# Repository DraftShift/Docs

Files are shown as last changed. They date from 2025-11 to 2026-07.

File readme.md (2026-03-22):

# DraftShift Documentation Source

This repository contains the source code for the DraftShift documentation website.

Visit [https://stealthchanger.com](https://stealthchanger.com) for the actual documentation.

---

## Contributing

We welcome contributions! If you'd like to help improve the documentation:

- Submit a descriptive [pull request](https://docs.github.com/en/pull-requests/collaborating-with-pull-requests/proposing-changes-to-your-work-with-pull-requests/creating-a-pull-request) of the feature/issue you are addressing.

- Keep the documented information concise.

### Contributing Build Guides

If you want to contribute build guides, please refer to the [Build Guide documentation](CONTRIBUTING_GUIDES.md) for more information.

### Development Setup

To run the documentation site locally:

1. **Prerequisites**: Ensure Python is installed and included in your environment PATH.

2. **Install dependencies**:
   ```
   pip install -r requirements.txt
   ```

3. **Run the development server**:
   ```
   python -m mkdocs serve
   ```

The site will be available at `http://127.0.0.1:8000` with live reload enabled.

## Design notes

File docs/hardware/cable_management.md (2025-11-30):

---
search:
  boost: 2 
---

## Umbilical Cables
An umbilical cable is required for each toolhead. They typically route from a [distribution board](../electronics/distro_boards.md) to a [toolhead board](../electronics/th_boards.md). On a StealthChanger, keeping the tool's umbilical in a controlled state is extremely important. If a tool's umbilical were to obstruct any of the other tools, it could result in a crash and cause a print failure. 

To help the umbilical move in a controlled fashion, we employ the use of a flat spring steel or piano wire. This addition gives the umbilical a controlled arc and helps it return to its resting position safely.

!!! tip "Spring Steel?"
    Flat spring steel (3x0.3mm) is the preferred aid for the tool's umbilical. It provides better lateral control and is what comes supplied as part of the LDO `Toolhead and Dock Kit`.

Umbilical Cables

## Fanny Pack
Originally by [ManCheetah](https://www.printables.com/@EddieSha_454383){:target="_blank"}, the Fanny Pack has been adopted by DraftShift Design as the de facto method of housing a [distribution board](../electronics/distro_boards.md) on the rear of the printer. Compared to the original, our updated version brings compatibility with a number of [distribution boards](../electronics/distro_boards.md) and buck converter options.

Fanny Pack

## Wire Duct
The Wire Duct serves as a conduit between the [Fanny Pack](#fanny-pack) and your printers electronics bay. Under its cover is an EMS compatible panel for you to mount any extra pieces you might need. 

Wire Duct

## Assembly
See the [Build Guides](../hardware/guides/cable_management/index.md) for assembly instructions.

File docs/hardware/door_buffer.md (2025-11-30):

---
search:
  boost: 2 
---

Door Buffer

## Context

### The Problem
To give the [Modular Docks](modular_dock.md) the maximum amount of rigidity, they need to be supported above and below. Adding an extrusion [crossbar](#crossbar) solves that problem but also introduces another. With the crossbar in line with the frame, the standard Voron V2 front-idlers collide with the crossbar and moving the extrusion outside of the frame would get in the way of mounting the door.

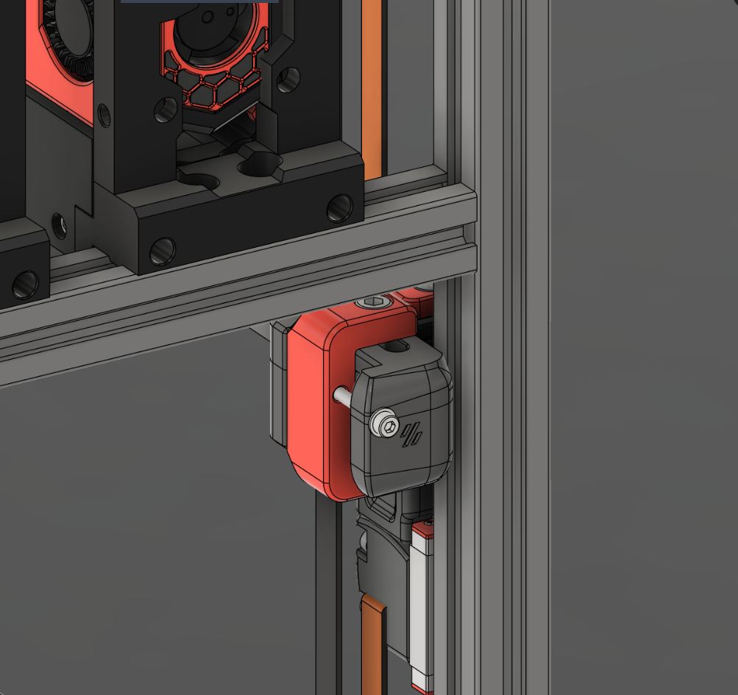
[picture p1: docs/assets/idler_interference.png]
Idler interference


### The Solution
Adding a Door Buffer provides a means to install the [crossbar](#crossbar) and retain the ability to mount the door on the front. The Door Buffer uses 3d printed pieces to fill the gaps around the front of the printers frame and adds new mounting points for the door.

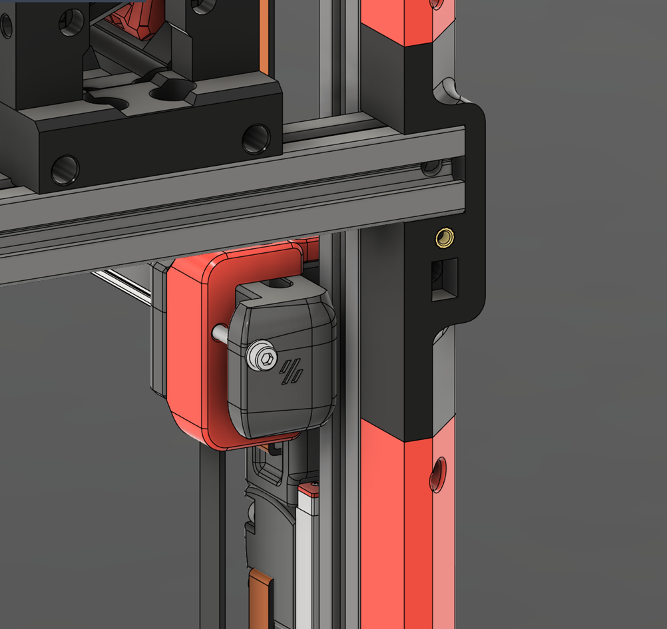
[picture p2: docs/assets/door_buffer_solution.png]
Door buffer solution


There are versions of the Door Buffer for both [standard Voron V2 doors](https://github.com/DraftShift/DoorBuffer/tree/main/STL/Stock%20Voron){:target="_blank"} and the [ClickyClack Fridge Door Mod](https://github.com/DraftShift/DoorBuffer/tree/main/STL/Clicky-Klack){:target="_blank"}, as well as options for [Micron](https://github.com/DraftShift/DoorBuffer/tree/main/STL/Micron){:target="_blank"}.

!!! info "Alternatives"
    You don't necessarily need to use printed pieces to act as a buffer. There are some other methods that the community uses.

    * **2020/1515 Extrusion** - Using blind joints you can mount extrusion to the front of the frame essentially making it 4020/3015.
    * **4020/3015 Extrusion** - Build the front of your printers frame using larger extrusion. 
    * **Mini/Micro BFI** - [Mini/Micro BFI](https://github.com/DraftShift/StealthChanger/tree/main/UserMods/BT123/MiniBFI%20%2B%20MicroBFI){:target="_blank"} takes a different approach and shortens the BFI idlers. This means the [crossbar](#crossbar) can be kept within the printers frame at the cost of less printable area and reduces the amount you can adjust the AB belts.

## Crossbar
The crossbar is a piece of extrusion mounted to the front of the printer’s frame, providing a rigid and stable attachment point for the [Modular Dock](modular_dock.md).

The crossbar should be made from extrusion that matches your printer, 2020 for Voron V2 or 1515 for Micron. The length of the crossbar changes depending on the size of your frame and which version of Door Buffer you are using.

| Printer | DraftShift Crossbar | LDO Crossbar |
| --- | --- | --- |
| Voron 250 | 400mm | 370mm |
| Voron 300 | 450mm | 420mm |
| Voron 350 | 500mm | 470mm |
| Micron 180 | 302mm | - |

!!! tip "Crossbar Adapter"
    You can use the DraftShift Door Buffer with LDO length extrusions by using an [adapter](https://github.com/DraftShift/DoorBuffer/tree/main/STL/Adaptor){:target="_blank"}.

!!! info "Monolith AWD"
    With Monolith protrusion the front motors would hit the crossbar even with the door-buffer. To work around that you can use one of the following usermods:

    - [printed adapter for door buffer with crossbar and Monolith AWD](https://github.com/DraftShift/DoorBuffer/tree/main/UserMods/MikeYankeeOscarBeta/Doorbuffer_Adapters){:target="_blank"}
    
    - [printed adapter for crossbar with doomcube 4040 frame and Monolith AWD](https://github.com/DraftShift/ModularDock/tree/main/UserMods/MikeYankeeOscarBeta/Monolith_Crossbar){:target="_blank"}

## Assembly
The assembly guide for the Door Buffer can be found in the [Build Guides](guides/door_buffers/index.md) section.

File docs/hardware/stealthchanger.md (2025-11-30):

---
search:
  boost: 2 
---

StealthChanger is the key component and namesake of the StealthChanger ecosystem. It can be broken down in to 2 main components, the [Shuttle](#shuttle) and [Backplate](#backplate), which allows the toolhead to be removed from the gantry and be docked so that another tool can be picked up. During operation, the mechanism also behaves like [Voron Tap](https://github.com/VoronDesign/Voron-Tap){:target="_blank"} and can be used for probing the bed.

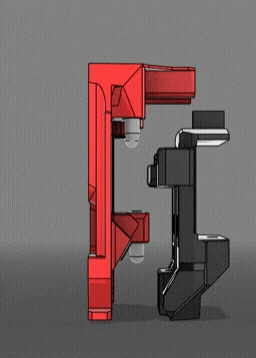
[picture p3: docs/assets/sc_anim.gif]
StealthChanger


## Shuttle
The StealthChanger Shuttle gets mounted to the gantry's X-rail MGN carriage and serves the purpose of being a receptacle for the [Backplate](#backplate). It uses bushings and magnets which allow the [Backplate](#backplate) to
kinematically attach to the gantry.

### Printed vs CNC
The printed and CNC versions of the Shuttle both operate in the same way. You can print the shuttle and source the bushings, magnet and screws or purchase a ready to go CNC shuttle. 

CNC Shuttles offer some QOL improvements like improved belt retention and in the case of LDO's Shuttle, precision-machined bushings.

When printing a Shuttle, it is important to note that the selection of material you use and your printers accuracy are important. Please reference the [Print Tuning Section](../getting_started.md#print-tuning) before printing your Shuttle.

!!! warning "ABS+"
    We have found that when used for StealthChanger, ABS+ tends to crack over time and advise against using it.

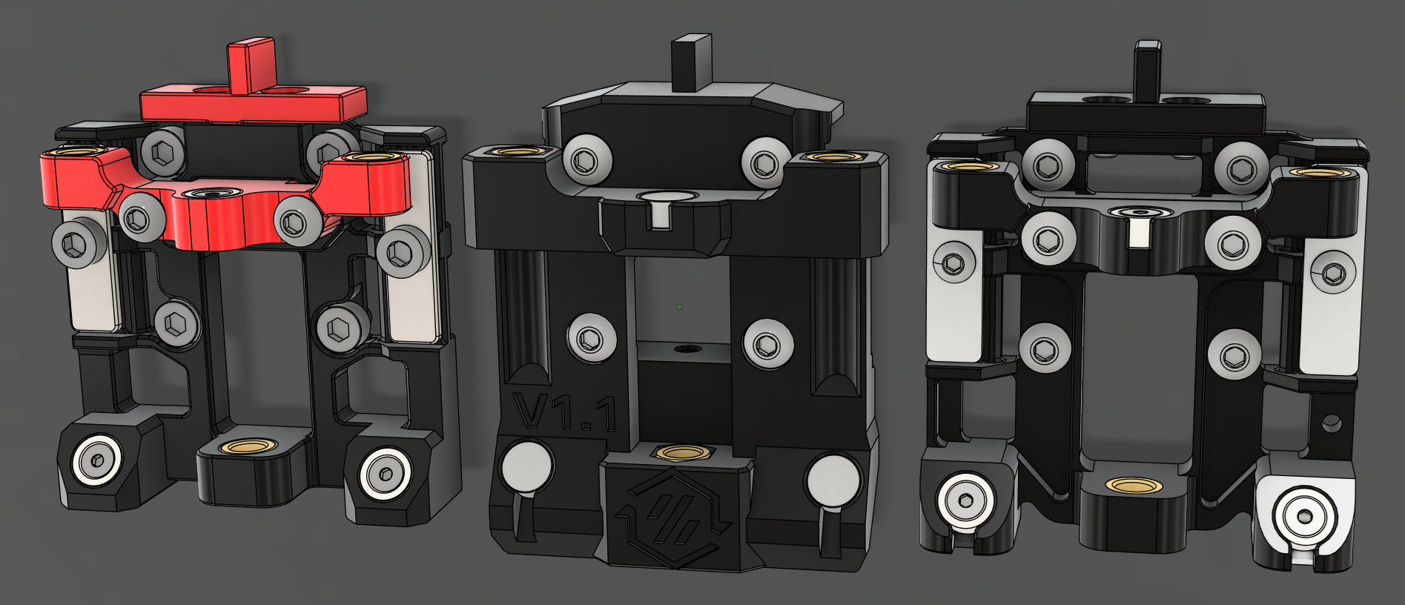
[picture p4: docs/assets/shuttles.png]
Shuttles


| Shuttle | MGN12 | MGN9 | Micron | 6mm Belt | 9mm Belt |
| :-: | :-: | :-: | :-: | :-: | :-: |
| Printed | :fontawesome-solid-check:{style="color:green;"} | :fontawesome-solid-asterisk:{style="color:orange;"} | :fontawesome-solid-asterisk:{style="color:orange;"} | :fontawesome-solid-check:{style="color:green;"} | :fontawesome-solid-asterisk:{style="color:orange;"} |
| CNC | :fontawesome-solid-check:{style="color:green;"} | :fontawesome-solid-xmark:{style="color:red;"} | :fontawesome-solid-xmark:{style="color:red;"} | :fontawesome-solid-check:{style="color:green;"} | :fontawesome-solid-check:{style="color:green;"} |

!!! asterisk "MGN9/Micron"
    The hole spacing on MGN9 is too small to clamp the belts reliably without the screws getting in the way. This means a Voron V2 with MGN9 on X axis or a Micron requires the use of the [Shuttle Keeper](#shuttle-keeper). 

!!! asterisk "9mm belts"
    9mm belts can be used with CNC Shuttles. If you want to use 9mm belts with a printed Shuttle, a [usermod by BT123](https://github.com/DraftShift/StealthChanger/tree/main/UserMods/BT123/Split%20Keeper){:target="_blank"} is required.

!!! info "Monolith and Inverted Belts"
    Inverted belts with printed shuttle require the use of this [usermod by BT123](https://github.com/DraftShift/StealthChanger/tree/main/UserMods/BT123/Split%20Keeper){:target="_blank"}.
    Inverted belts can be mounted to CNC Shuttle as is, but with [Monolith](https://github.com/Monolith3D/Monolith_Gantry/tree/main){target="_blank"} this results in slight angled belt-path. To get a straight belt path with CNC-shuttle you can either use [belt-lock](https://github.com/MikeYankeeOscarBeta/belt_lock){:target="_blank"} or this [XY-joint mod by dderg](https://github.com/Monolith3D/Monolith_Gantry/tree/main/UserMods/dderg/XY%20Joints%20compatible%20with%20Fysetc%20CNC%20Stealthchanger%20Shuttle){:target="_blank"}.

## Shuttle Keeper
The Shuttle Keeper is an additional component that can be used to hold the belts in place while the [Shuttle](#shuttle) is removed from the MGN Rail. There are situational reasons as to when and why you would want to use a Shuttle Keeper. See the below list for details.

* Only compatible with a printed [Shuttle](#shuttle).
* Required for a MGN9 [Shuttle](#shuttle).
* Optional for a MGN12 [Shuttle](#shuttle).
* Shuttle Keeper moves the toolhead forward 5-6mm.

Shuttle Keeper

## Belt Helper
Belt helper is a tool that will hold your belts for you while installing the [Shuttle](#shuttle). Once attached to the belts, the Belt Helper will assist in pulling the belts into position for the [Shuttle](#shuttle) to clamp them.

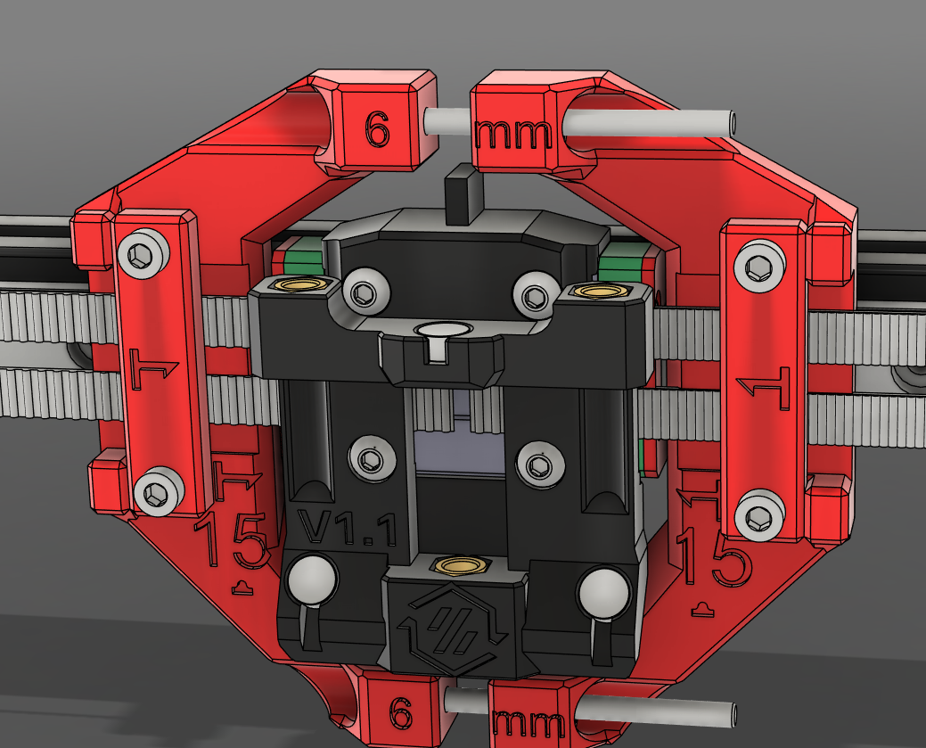
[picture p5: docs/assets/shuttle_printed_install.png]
Shuttle Install


!!! tip "One Tool to Rule Them All"
    The Belt Helper was designed to assist with installing the printed [Shuttle](#shuttle). It can also be useful with CNC shuttles to give you that extra set of hands you always wanted.

!!! info "Mini/Micro BFI"
    If using [Mini/Micro BFI](https://github.com/DraftShift/StealthChanger/tree/main/UserMods/BT123/MiniBFI%20%2B%20MicroBFI){:target="_blank"}, the Belt Helper is required to pre tension your belts to a point where your idlers only need minimal adjustment.

## Backplate
The StealthChanger Backplate is the companion component to the [Shuttle](#shuttle). Each compatible toolhead has its own unique Backplate that gets attached to the tool. The backplate is a critical component of StealthChanger and requires you to ensure you have good print accuracy, especially when pairing with a CNC Shuttle. Please reference the [Print Tuning Section](../getting_started.md#print-tuning) before printing your Backplate. For a list of compatible tools, see the [Toolheads](toolheads.md) page.

Backplate

## Assembly
See the [Shuttle Build Guides](guides/shuttles/index.md) and [Backplate Build Guides](guides/backplates/index.md) sections for assembly instructions.

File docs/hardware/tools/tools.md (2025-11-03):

For the purposes of StealthChanger the toolhead selection is rather important. It is often the deciding factor in how the rest of the build is configured. It determines which docks you can use, the maximum number of tools you can use, and the can also have a large impact on power requirements.

???+ info "Printing"
    Officially supported toolheads do not require modification to work with StealthChanger, only the addition of the Stealthchanger backplate and possibly a spacer. Each toolhead can be sourced from their respective repositories. Toolheads that are not officially supported will require modification to work with StealthChanger and will be marked as a usermod.

??? info "Extruders"
    * You can use any extruder you want as long as it is supported by the toolhead of your choice.
    * It's important to note that the width of the extruder may impact the maximum tool count as it may render the tool width wider, potentially limiting the total number of tools that can be accommodated.
    * :warning: Pay attention to the tensioning screw on the extruder, it may collide with the tool beside it if it extends outside the tool's width and there is not enough room between them.

??? info "Hotends"
    * Choose whichever hotend you like, as long as the toolhead supports it, you can use it.
    * :warning: Some high-flow hotends may require significant tuning to prevent oozing while moving to, and from the dock.

??? tip "Community Recommendation"
    Anthead is the recommended toolhead due to its integrated magnets in the fan ducts, which enhance stability during the docking process. Other tools can achieve similar results, but may require additional modifications.

<div class="grid cards" style="text-align: center;" markdown>

{% for tool, tool_data in toolheads.items() %}
    {% set v250 = max_tools[tool_data.dock_width][250]|string if max_tools[tool_data.dock_width][250] > 0  else '-' %}
    {% set v300 = max_tools[tool_data.dock_width][300]|string if max_tools[tool_data.dock_width][300] > 0  else '-' %}
    {% set v350 = max_tools[tool_data.dock_width][350]|string if max_tools[tool_data.dock_width][350] > 0  else '-' %}
    {% set m180 = max_tools[tool_data.dock_width][180]|string if max_tools[tool_data.dock_width][180] > 0  else '-' %}
-   <span id="{{ tool.replace(' ', '_').lower() }}"></span>

    ### {{ tool }}

    {{ tool }}

    **Author:** {{ tool_data.author }}

    **Dock Width:**{ title="Standard: 60mm<br>Wide: 76mm" } {{ tool_data.dock_width.capitalize() }}

    **Short Dock:**{ title="The height of the dock (Z axis) being less than standard. For Voron printers, the shorter height is not available for larger toolheads. Compatibility with Door Buffer varies depending on toolhead configuration. For Micron printers the short variant is a requirement." } {{ ':fontawesome-solid-check:{ style="color:green;" }' if tool_data.short_dock else ':fontawesome-solid-xmark:{ style="color:red;" }' }}

    **Stubby Dock:**{ title="The depth of the dock (Y axis) being less than standard and is not compatible with Door Buffer and is only available for the smaller toolheads." } {{ ':fontawesome-solid-check:{ style="color:green;" }' if tool_data.stubby_dock else ':fontawesome-solid-xmark:{ style="color:red;" }' }}

    | Size | Max Tools |
    |--------------|------------|
    | 250mm Voron  | {{ v250 }} |
    | 300mm Voron  | {{ v300 }} |
    | 350mm Voron  | {{ v350 }} |
    | 180mm Micron | {{ m180 }} |

    [:fontawesome-brands-github: View on GitHub]({{ tool_data.url }}){:target="_blank" .md-button}

{% endfor %}

</div>

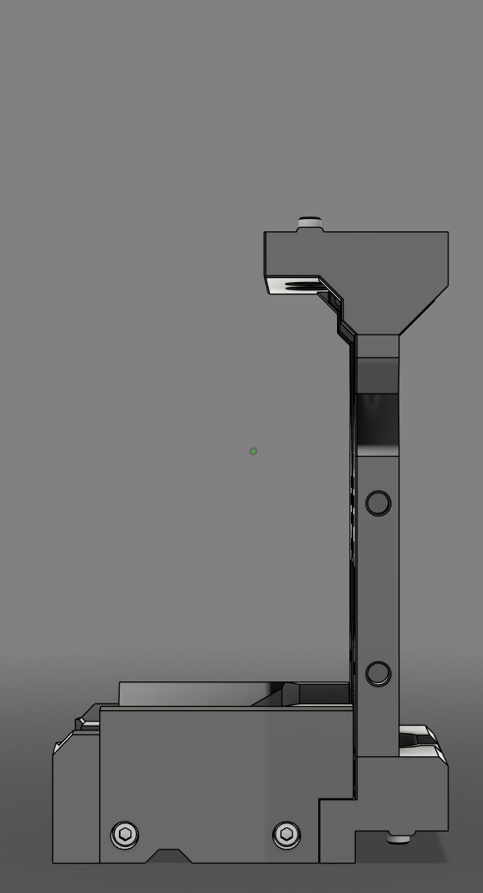
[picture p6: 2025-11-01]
docs/assets/dock_z-short_y-standard.png

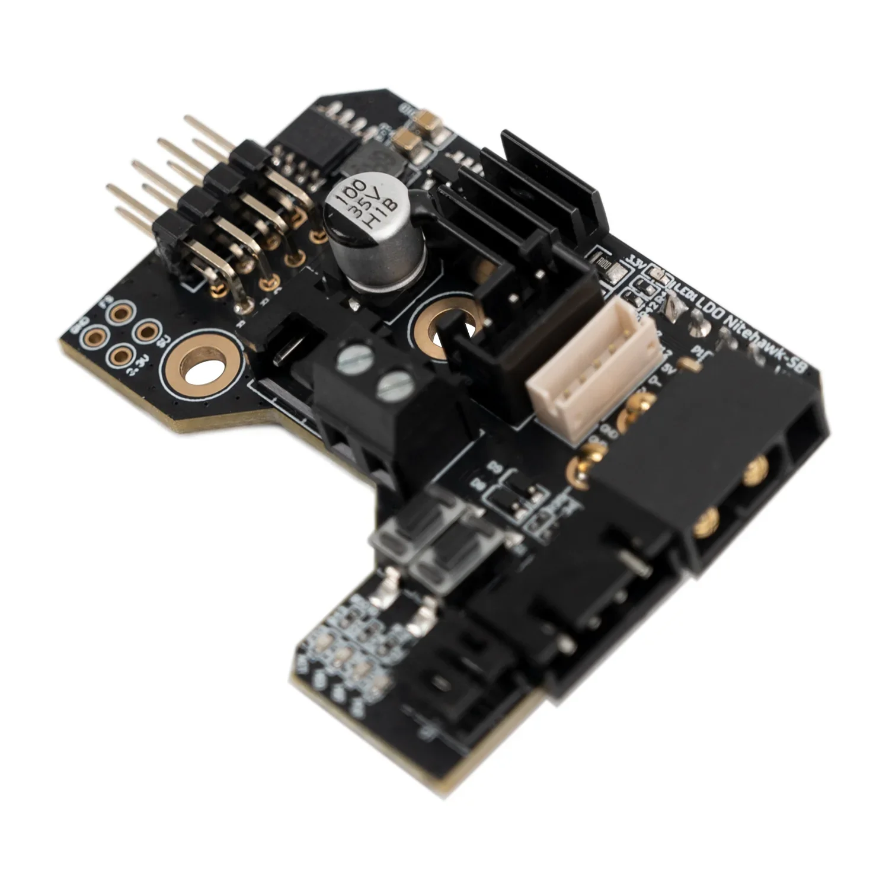
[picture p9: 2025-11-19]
docs/assets/tool_boards/nitehawk_sb.webp

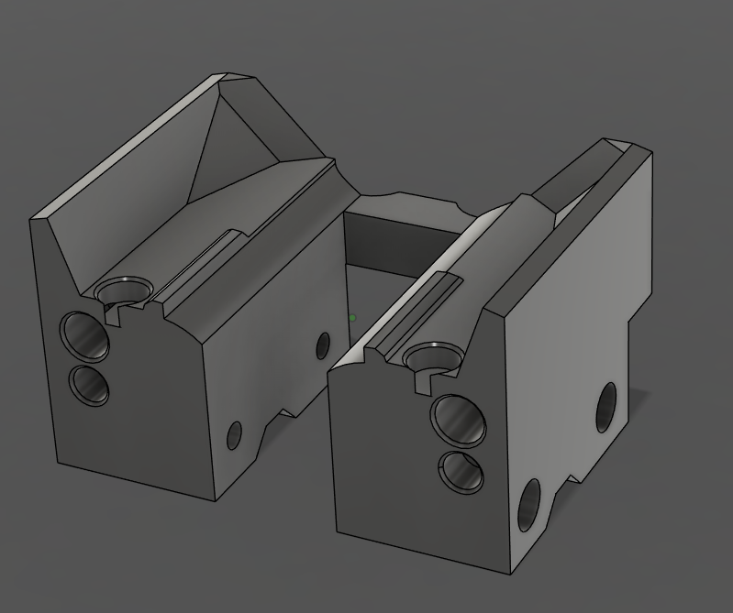
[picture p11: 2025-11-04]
docs/assets/dock-base_stubby.png

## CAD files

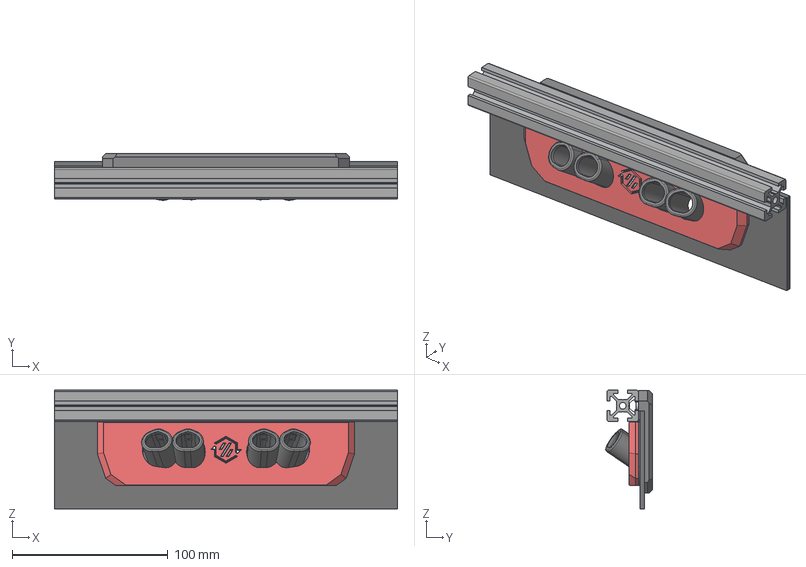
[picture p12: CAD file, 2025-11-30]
step_files/Cable Mangement/Umbilical Plate.step
220.0 x 29.9 x 76.1 mm
Frame
Foam Tape (1mm) (1) (3)
Face Plate_part
Logo Insert_part
Hexes_part
Outer_part
1mm Foam
M3 Threaded Insert (3) (8) (1) x 4
M3x10 SHCS (7) x 4
2020 Drop-in T-nut, M5 (8)
2020 Drop-in T-nut, M5 (7)
M5x10 BHCS (1) x 2

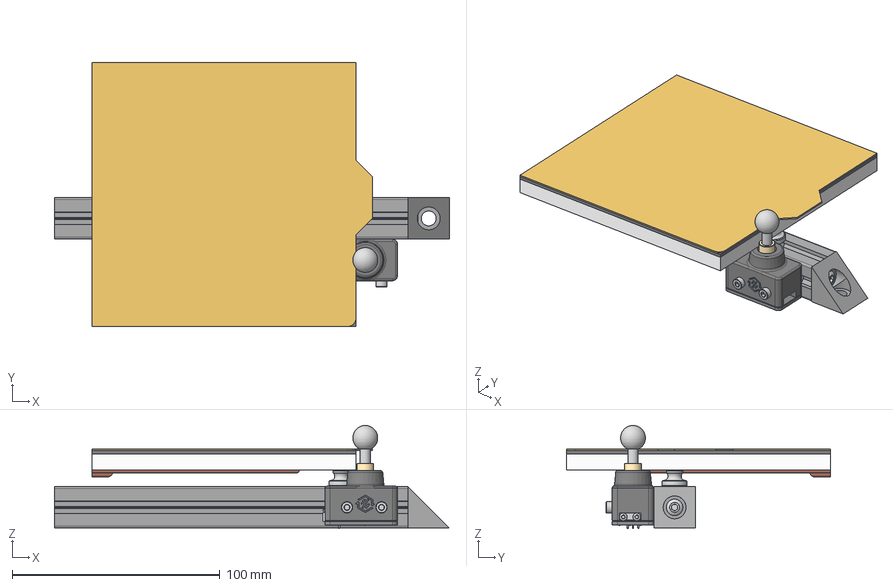
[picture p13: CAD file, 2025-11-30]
step_files/Calibration/Sexball_Probe.step
190.0 x 127.0 x 49.6 mm
Endstop Block
Omron_D2F_F
JST - XH - Thru (R) - 3Pin - 2.54mm
M2x10 STS_1
M2x10 STS_2
M3x20 SHCS
M3x20 SHCS_1
hammerhead nut v1
hammerhead nut v1 (1)
Shaft
Ball
8x10x5mm Bushing
10in MIC6 Plate
Magnet Sheet
Flex Sheet
Bed heater
M4 Knurled Nut DIN 466-B
M3x16 SHCS (2)
M5x16 BHCS (21)
2020 Drop-in T-nut, M3
HFSB5-2020-370-TPW (9)
90deg Corner (OpenBuilds)

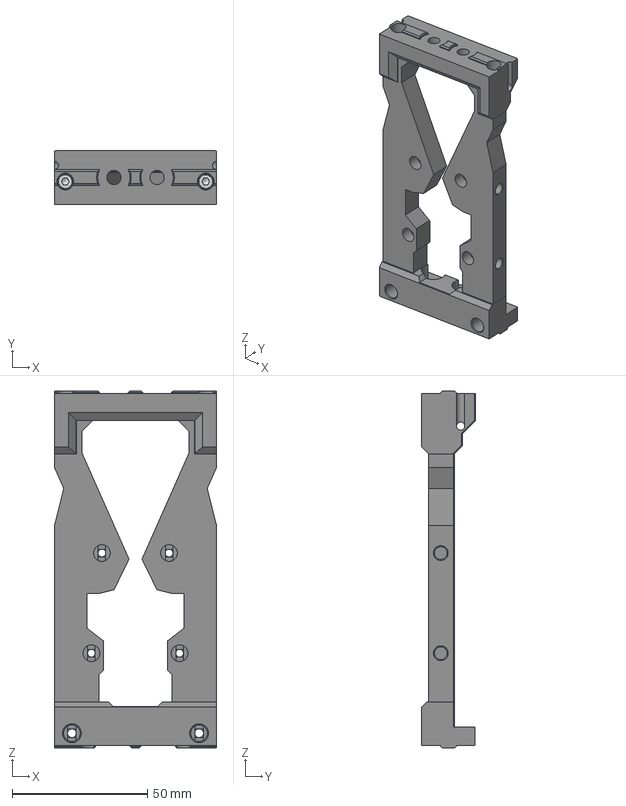
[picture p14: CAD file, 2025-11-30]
step_files/Docks/Frame - 2020 Short.step
60.0 x 20.0 x 132.2 mm
M3 Threaded Insert (3)_1_2 x 4
M3x16 SHCS x 4
Bottom
Top
Left (1)
Right (1)
M3 Threaded Insert (3)_1_1 x 2

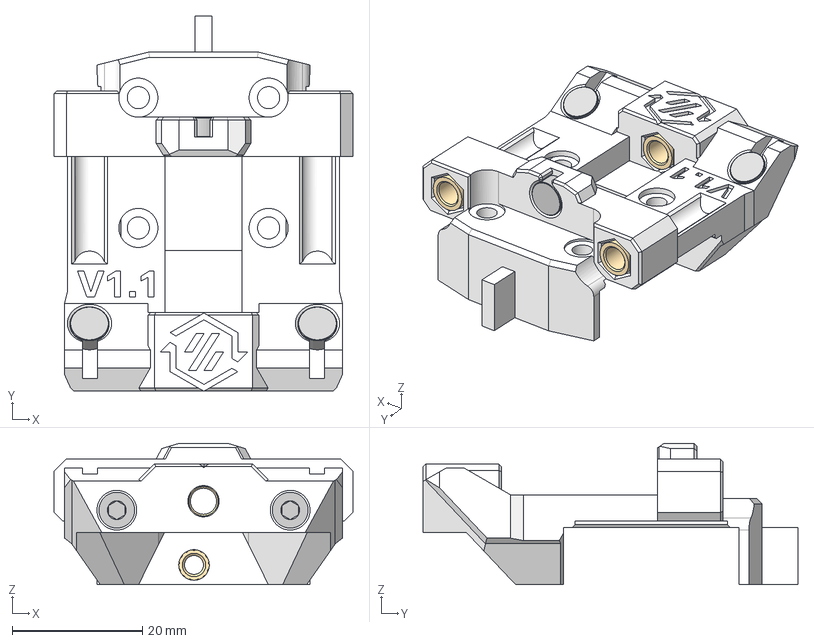
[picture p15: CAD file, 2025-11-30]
step_files/Shuttles/Shuttle_MGN12.step
45.9 x 57.5 x 21.7 mm
Shuttle MGN12
Bushings x3
6x3mm Magnets x3
(Unsaved)
M3x40 SHCS

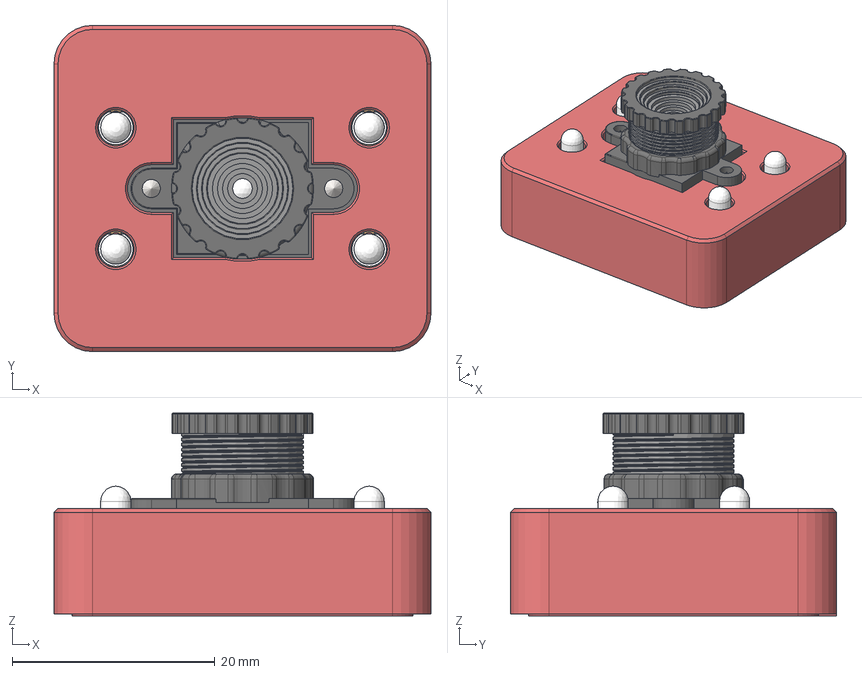
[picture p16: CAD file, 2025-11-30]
step_files/Usermods/Axiscope_Camera.step
37.2 x 32.2 x 20.0 mm
Copy of SOT 23^OV9726 Camera module x 3
Copy of 0402c_2320560^OV9726 Camera module x 28
cross fh tapping 7976_din_Tapping screw DIN 7982-ST2.2x4.5-C-H-N x 2
Copy of TSOP-6^OV9726 Camera module
Copy of QFN36 6x6^OV9726 Camera module
Copy of sm04b-srss-tb_lf__sn_^OV9726 Camera module
Copy of tsop8^OV9726 Camera module
Case Upper
Case Lower
6x3 Magnet x 4
LED x 4
Diode Silkscreen
LED Bulbs

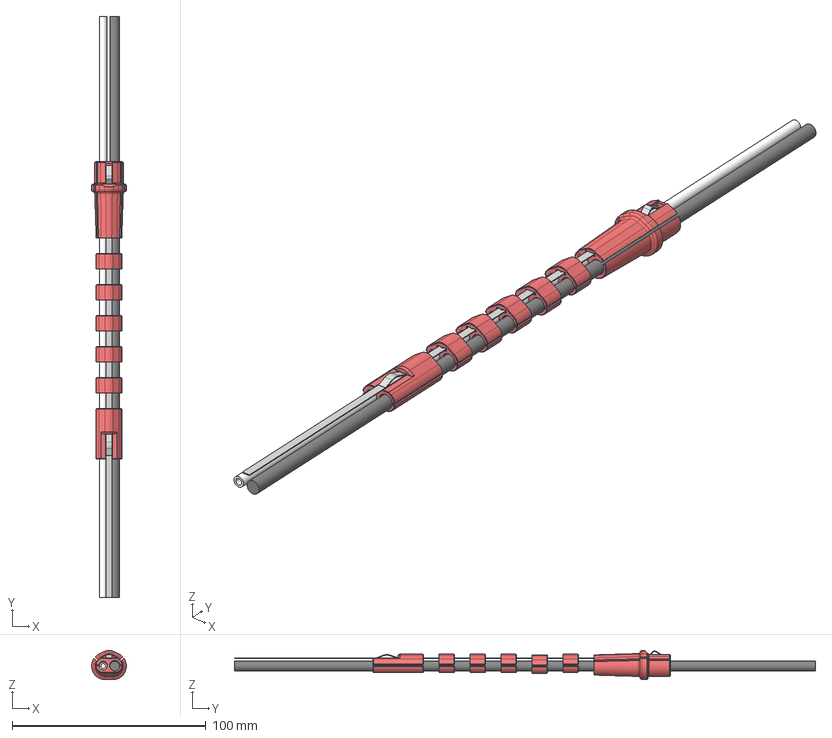
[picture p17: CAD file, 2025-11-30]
step_files/Cable Mangement/Umbilical.step
18.0 x 300.0 x 15.1 mm
[tpu]_Relief_Voron_x5xN_part
[tpu]_Terminator_Voron_xN_part
[tpu]_Clip_Voron_xN_part
Spring Steel Bend
[tpu]_Clip_Voron_xN_part_1
Wire
PTFE
[tpu]_Clip_Voron_xN_part_2
[tpu]_Clip_Voron_xN_part_3
[tpu]_Clip_Voron_xN_part_4
Spring Steel

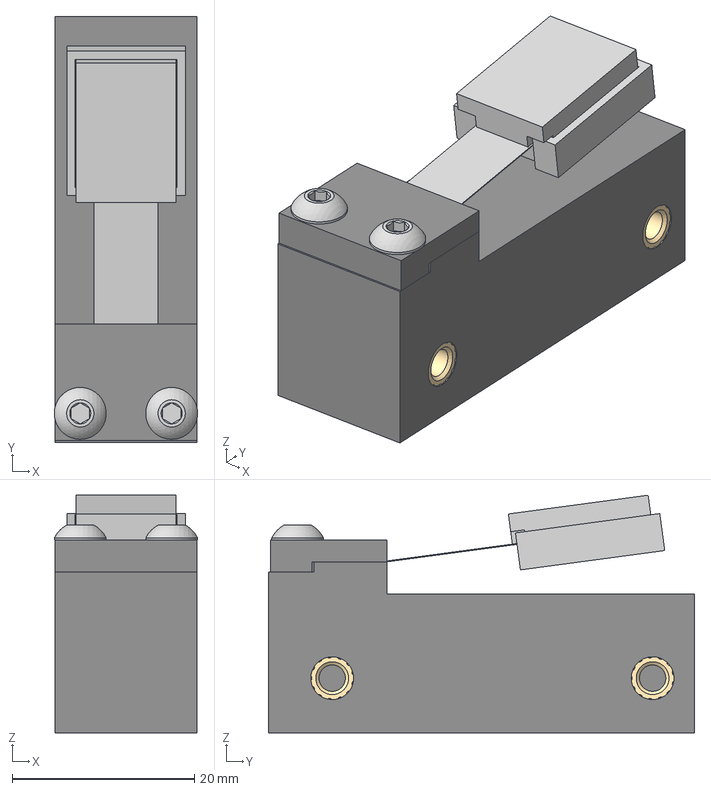
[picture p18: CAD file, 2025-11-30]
step_files/Docks/Blocker - Spring Steel.step
15.7 x 46.8 x 26.1 mm
Clamp
Silicone Jig
(Unsaved) x 6
M3x8 BHCS x 2
Spring Steel Body
Spring Steel Blocker
Silicone

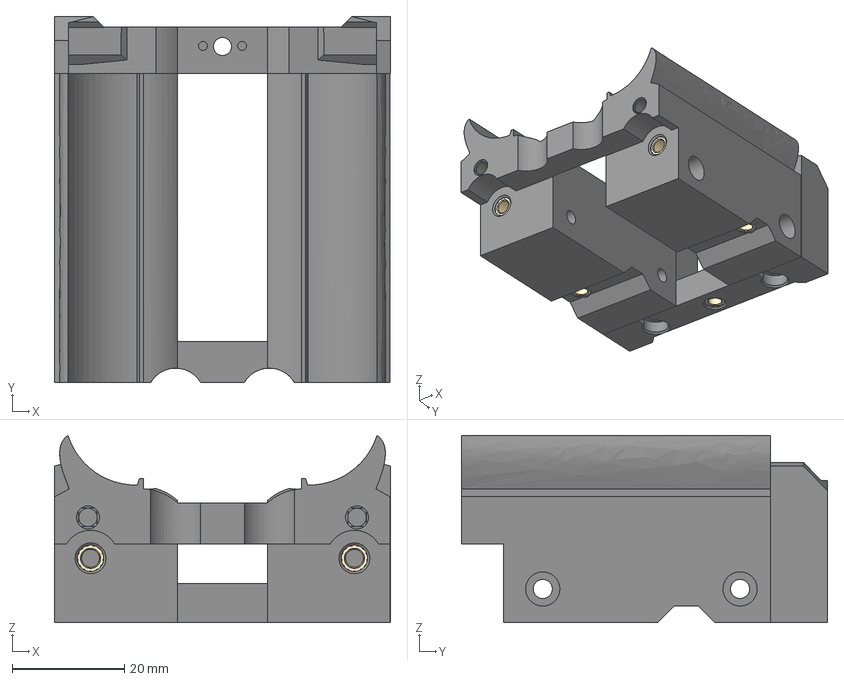
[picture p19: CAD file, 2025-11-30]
step_files/Docks/Base - DragonBurner.step
60.0 x 65.3 x 33.4 mm
M3 Threaded Insert (3) (8) (1) x 6
Base (1)
Back (5)
M3 Threaded Insert (3) (8) (1)_1

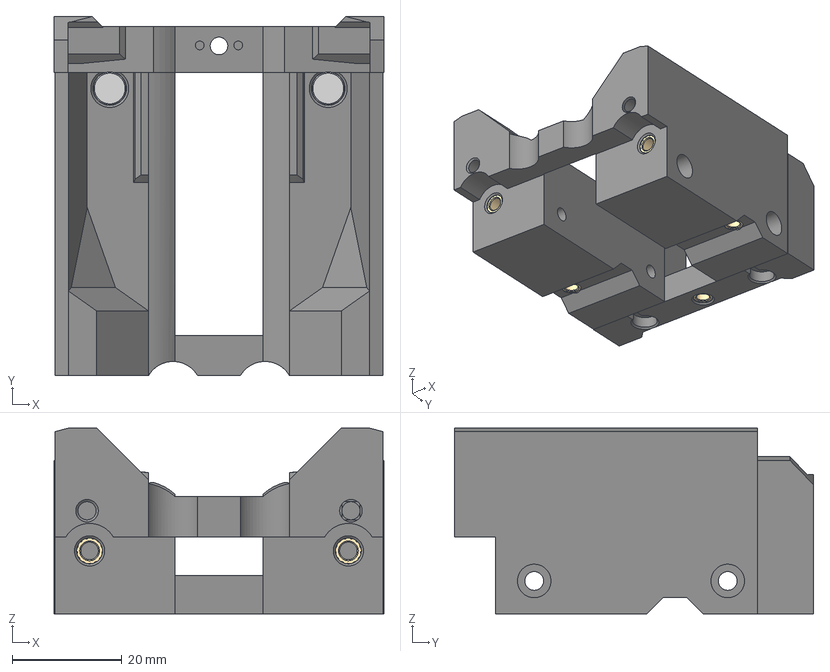
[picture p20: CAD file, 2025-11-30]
step_files/Docks/Base - Anthead.step
60.0 x 65.3 x 33.8 mm
Back (1)
Base (7)
M3 Threaded Insert (3) (8) (1) x 6
6x3mm Magnet (1)
6x3mm Magnet
M3 Threaded Insert (3) (8) (1)_1

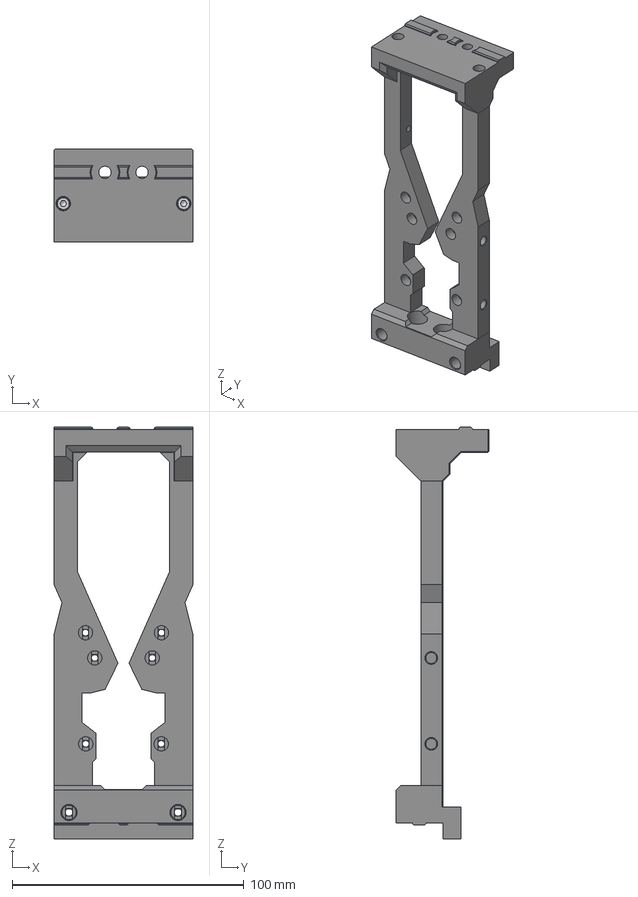
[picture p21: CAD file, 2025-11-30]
step_files/Docks/Frame - Crossbar.step
60.0 x 40.0 x 177.9 mm
M3x16 SHCS x 4
M3 Threaded Insert (3)_1_1 x 6
Left
Right
Bottom Crossbar
Top Crossbar

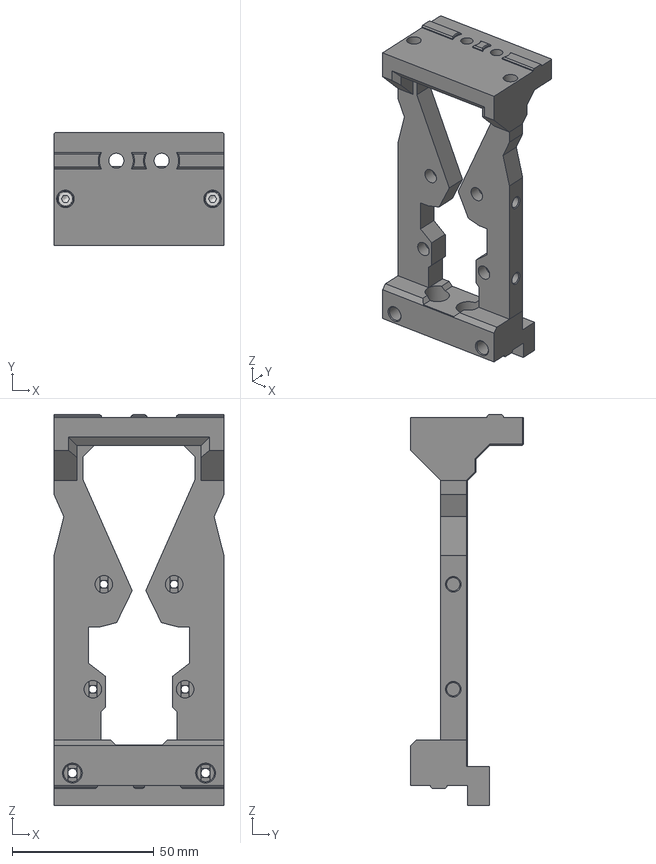
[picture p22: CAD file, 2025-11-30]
step_files/Docks/Frame - Crossbar Short.step
60.0 x 40.0 x 138.2 mm
M3x16 SHCS x 4
M3 Threaded Insert (3)_1_1 x 2
Left (1)
Right (1)
Bottom Crossbar
Top Crossbar
M3 Threaded Insert (3)_1_2 x 4

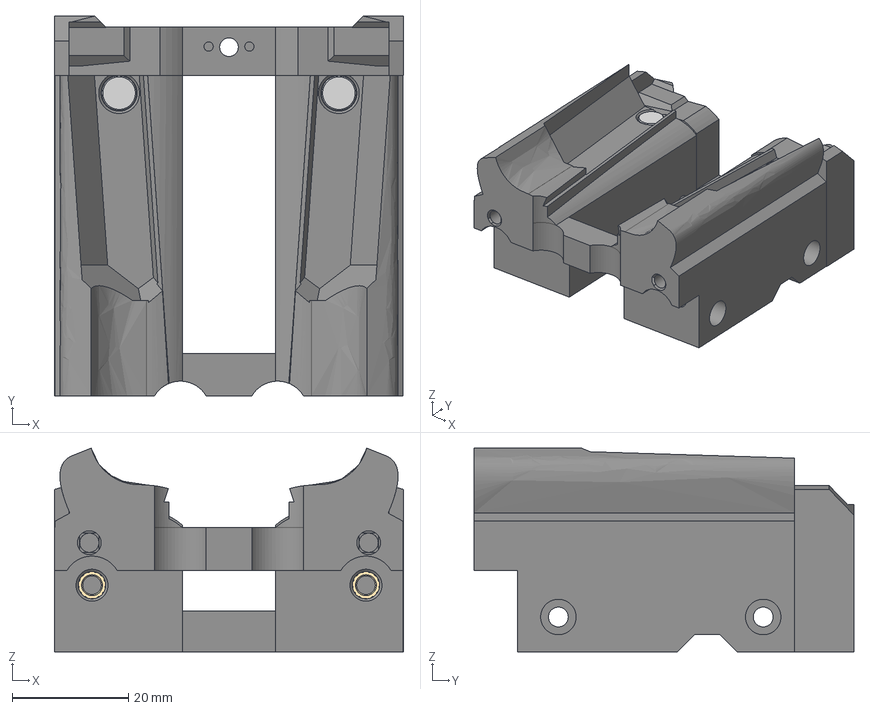
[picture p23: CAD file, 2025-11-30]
step_files/Docks/Base - Yavoth.step
60.0 x 65.3 x 35.0 mm
M3 Threaded Insert (3) (8) (1) x 6
6x3mm Magnet (1) (1)
6x3mm Magnet (2)
M3 Threaded Insert (3) (8) (1)_1
Base (1) (1)
Back (5) (1)

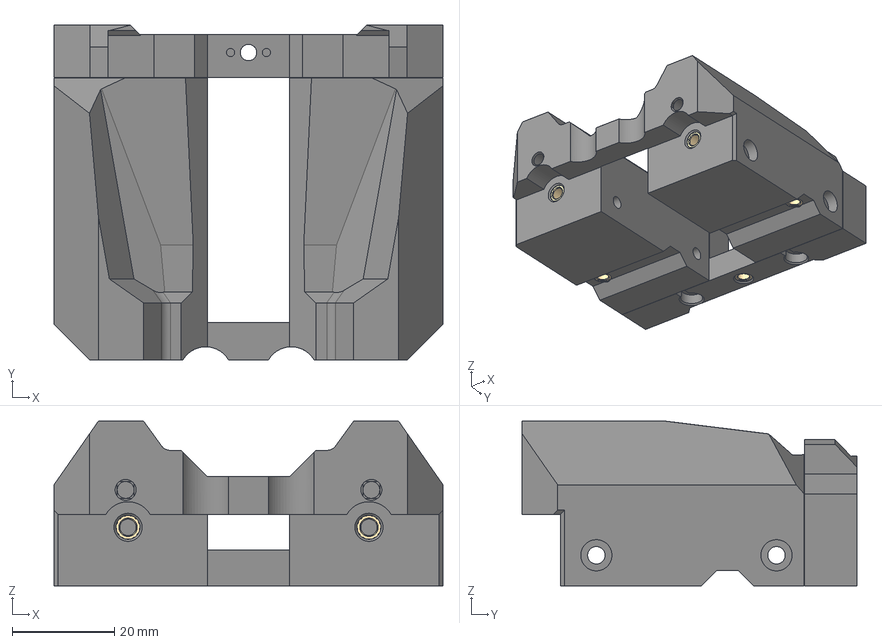
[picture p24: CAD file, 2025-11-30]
step_files/Docks/Base - A4T.step
76.0 x 65.4 x 32.2 mm
Base (2) (1) (1)
Back (3) (1) (1)
M3 Threaded Insert (3) (8) (1) x 4
M3 Threaded Insert (3) (8) (1)_1 x 2
M3 Threaded Insert (3) (8) (1)_1_1

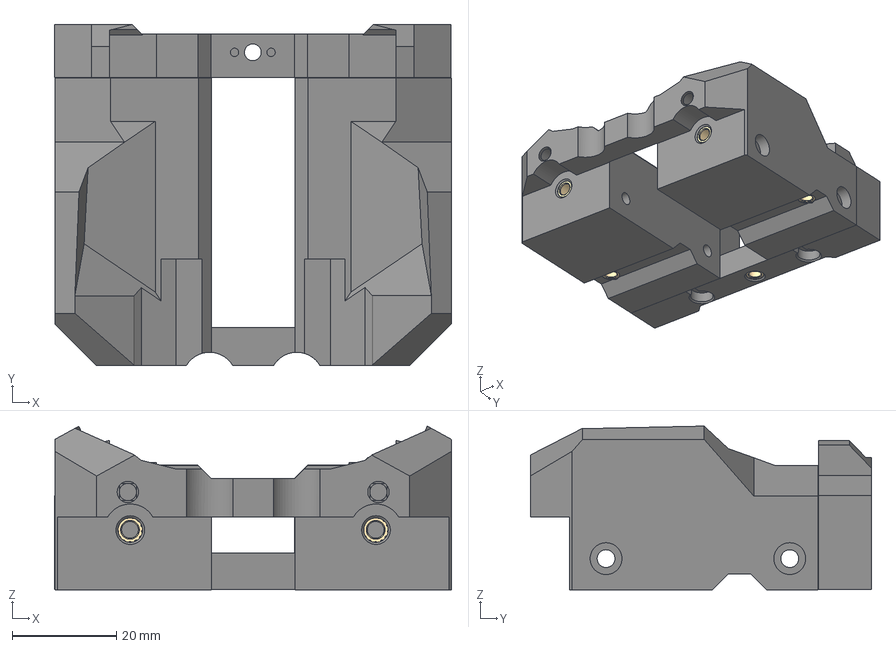
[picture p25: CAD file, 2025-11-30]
step_files/Docks/Base - StealthBurner.step
76.1 x 65.4 x 31.4 mm
M3 Threaded Insert (3) (8) (1) x 4
M3 Threaded Insert (3) (8) (1)_1 x 2
M3 Threaded Insert (3) (8) (1)_1_1
Back
Base

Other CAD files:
step_files/Docks/Base - JabberWocky.step
step_files/Docks/Base - BlackBird.step
step_files/Docks/Base - Mini StealthBurner.step
step_files/Docks/Blocker - Cup.step
step_files/Docks/Base - XOL.step
step_files/Docks/Frame - 2020.step

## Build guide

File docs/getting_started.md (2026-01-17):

# Getting Started

Before diving into your own StealthChanger build, please read the sections below — each covers essential information to ensure a successful and safe build. 

## Printing
All parts for StealthChanger should be printed using the Voron printing recommendation, except the 3d printed shuttle which also requires supports.

* `Layer Height` - 0.2mm
* `Extrusion Width` - 0.4mm, forced
* `Infill Percentage` - 40%
* `Infill Type` - Grid, Gyroid, honeycomb, Triangle or Cubic
* `Wall Count` - 4
* `Solid Top/Bottom Layers` - 5
* `Layer Height` - 0.2mm
* `Supports` - As required

## Print Tuning
Your printer needs to print dimensionally accurate parts due to the tolerances required when meshing multiple pins and bushings together.
It is highly recommended that before printing the shuttle and tool back plates for StealthChanger, your printer and filament be tuned for dimensional accuracy. 

!!! info "But but but, my prints look great!"
    Dimensional accuracy is often overlooked when our printers are making amazing looking parts. If you experience any binding or resistance while meshing the StealthChanger backplate to the shuttle, most often it is dimensional accuracy that is the culprit. This becomes even more evident when combining CNC shuttle with a printed tool back plate. 
    
    Many have found great success using [Califlower](https://vector3d.shop/products/califlower-calibration-tool-mk2){:target="_blank"} or one of its [derivatives](https://www.printables.com/search/models?q=califlower){:target="_blank"} to achieve the required dimensional accuracy for these high tolerance pieces.

## Losses
The addition of more tools and docks inside the printer typically means you end up with some lost printable build-volume. There should not be much loss in XY bed space, but whenever printing underneath the dock there is limited Z travel. These losses vary based on the printer’s configuration, as well as the selected tool and dock.

!!! info "So I can just increase the size of my Z axis to get rid of losses?"
    Increasing the height of the printer is often the first thing that comes to mind when trying to maintain the full printable area, unfortunately it also requires increasing the length of the umbilical for each tool which can become troublesome.

    If you require 100% of your build area, consider instead extending the printer in the Y axis. This will move the docks outside of the printable area of the bed and keep the umbilical at a shorter length as they only need to reach past the bed while at the top of the machine where there is more slack. These extended-Y Vorons have been dubbed [Vorlong](https://github.com/DraftShift/StealthChanger/tree/main/UserMods/TheSin-/Vorlong_%2B100y){:target="_blank"}.

## Community
StealthChanger has an active and helpful community on both [Discord](https://discord.gg/draftshift) and [facebook](https://www.facebook.com/groups/449879874593718/), if you get stuck at any point, don't hesitate to reach out and ask for help.

!!! info "User Mods"
    There are many [usermods](https://github.com/DraftShift/StealthChanger/tree/main/UserMods){target="_blank"} that can modify or enhance the many aspects the StealthChanger ecosystem. If you can't find what your after in the main repository, it's likely that one of our talented community members has created a user mod for it.

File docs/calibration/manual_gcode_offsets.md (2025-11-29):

{% macro code_block(lines="8 9 10") %}
``` cfg title="[tool Tn] example." hl_lines="{{ lines }}"
  [tool T1]
  tool_number: 1 # change to the index of the tool. 0, 1, 2, etc.
  extruder: extruder1 # change to match the extruder you are configuring: extruder, extruder1, etc.
  fan: T1_part_fan
  params_park_x: 0 # The absolute X-position of the tool in its dock.
  params_park_y: 0 # The absolute Y-position of the tool in its dock.
  params_park_z: 0 # The absolute Z-position where the tool and shuttle mate in the dock, determined when the TAP (or Z-probe) triggers.
  gcode_x_offset: 0 # The X-Axis offset of the nozzle's orifice in relation to tool 0
  gcode_y_offset: 0 # The Y-Axis offset of the nozzle's orifice in relation to tool 0
  gcode_z_offset: 0 # The Z-Axis offset of the nozzle's orifice in relation to tool 0
```
{% endmacro %}

Manual calibration uses a paper test to measure Z-offsets between tools.

!!! note "Critical"
    - Only home or probe with T0 during this calibration

### G-code Z Offset

{{ code_block(lines="10") }}

1. Ensure **T0 is on the shuttle**
2. Run: `INITIALIZE_TOOLCHANGER`
3. Home the printer: `G28`.
4. Level the gantry: `QUAD_GANTRY_LEVEL`.
5. Home Z again: `G28 Z`.
6. Raise the nozzle 10mm: `G1 Z10 F600`.
7. Manually remove the current tool and place the next tool on the shuttle
8. Perform a [manual paper test](#manual-paper-test) and adjust Z until you feel slight resistance
9. Once satisfied, run `M114` and copy the Z value from the console.
10. Update the `gcode_z_offset` value in [[tool Tn]](../software/ktc-easy/configuration/tool.md#tool) section of the [tool's config](../software/ktc-easy/configuration/tool.md) file.
11. Repeat from **step 6** for all remaining tools
12. Run: `FIRMWARE_RESTART`

### Manual Paper Test

The “paper test” involves placing a standard sheet of paper between the build plate and the nozzle, then carefully jogging the nozzle downward until you feel slight resistance as the paper is moved back and forth.

!!! tip "Key Points"
    - Use regular copy paper (approximately 100 microns / 0.1mm thick).
    - Always perform the test at **room temperature** with the nozzle and bed cold.
    - Ensure the nozzle and bed are clean and free of debris.
    - Use the same surface that you typically print on.

1. Cut a small piece of paper (approximately 5x3 cm).
2. Place it between the nozzle and bed.
3. Using manual movements (Mainsail/Fluidd/KlipperScreen), jog the nozzle down in small increments.
4. Push the paper back and forth to feel for resistance.
5. Continue until you feel slight friction where the paper slides, but with some resistance.

### G-code XY Offsets

{{ code_block(lines="8 9") }}

Calibrating XY offsets manually, involves doing test prints, visually examining the alignment and adjusting between tests. This procedure gets repeated until you are happy with the alignment.

- For manual XY calibration we recommend first using the [IDEX calibration tool](https://www.printables.com/model/201707-x-y-and-z-calibration-tool-for-idex-dual-extruder){target="_blank"} to get each tool's nozzle aligned to T0. 
- Follow that up with the [StealthChanger Logo Test Chip](https://www.printables.com/model/1092898-stealthchanger-logo-test-chip){target="_blank"} to ensure all offsets are working harmoniously.

<iframe src="https://www.printables.com/embed/201707" width="300" height="340" scrolling="no" frameborder="0"></iframe>
<iframe src="https://www.printables.com/embed/1092898" width="300" height="340" scrolling="no" frameborder="0"></iframe>

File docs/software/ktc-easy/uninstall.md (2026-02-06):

This guide covers the complete removal of klipper-toolchanger from your printer. Follow the steps below to delete the repository and clean up any leftover symlinks in Klipper.

## Remove Klipper-Toolchanger
Connect to the printer via SSH and enter the following commands:

``` bash { .copy }
cd ~/
ls
```

This will list the installed extension folders. Identify the correct toolchanger folder to remove. In this example we uninstall `klipper-toolchanger`:

``` bash { .copy }
sudo rm -rf ~/klipper-toolchanger/
```

!!! warning "Double-check the folder name"
    `rm -rf` will permanently delete the folder without confirmation.

## Clean Up Broken Symlinks
Delete the broken symlinks that still exist in `~/klipper/klippy/extras/`:

``` bash { .copy }
cd ~/klipper/klippy/extras/
ls
```
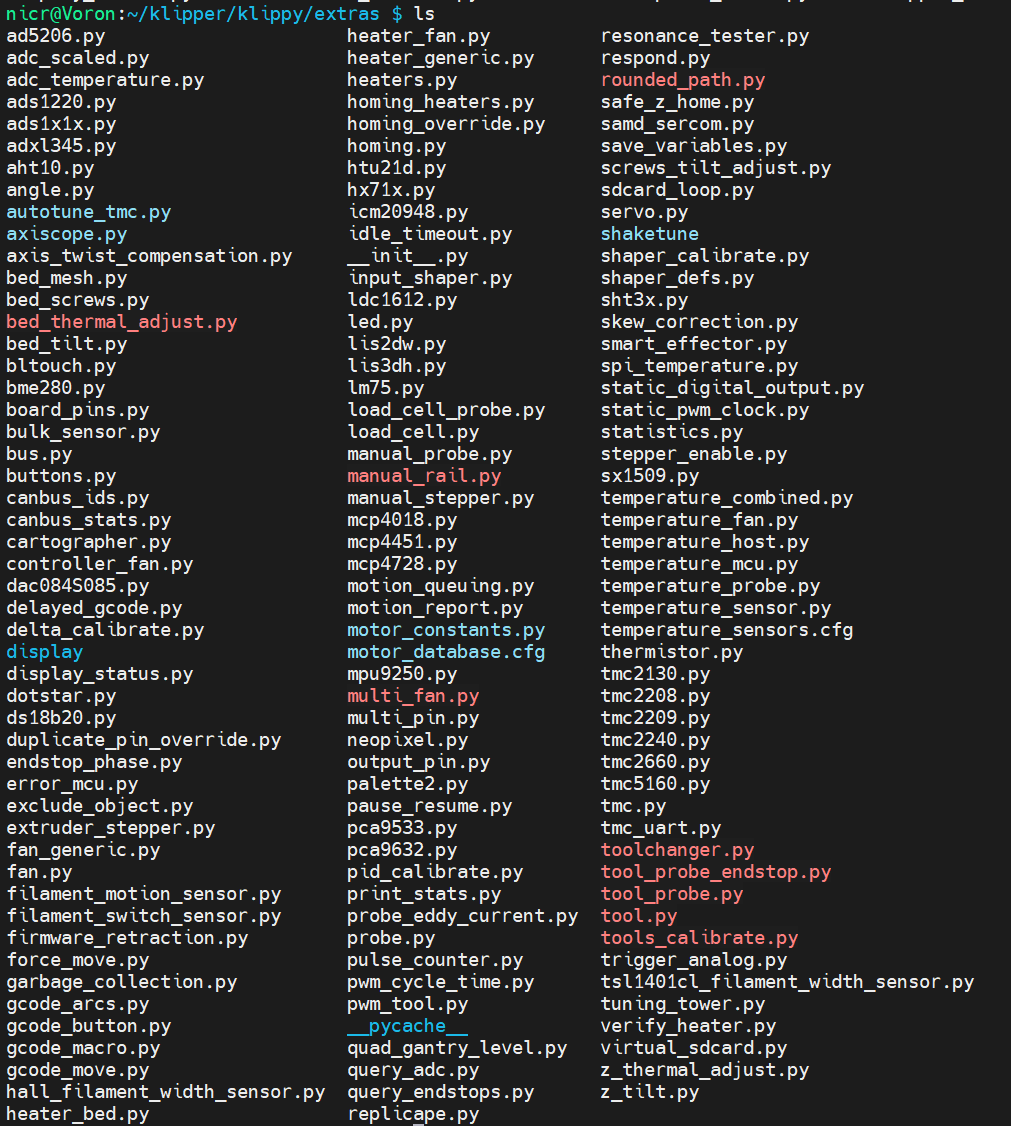
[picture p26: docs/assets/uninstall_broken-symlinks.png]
broken symlinks example


The files shown in red are broken links and can be safely removed:

``` bash { .copy }
sudo rm -f ~/klipper/klippy/extras/bed_thermal_adjust.py \
      ~/klipper/klippy/extras/multi_fan.py \
      ~/klipper/klippy/extras/manual_rail.py \
      ~/klipper/klippy/extras/rounded_path.py \
      ~/klipper/klippy/extras/toolchanger.py \
      ~/klipper/klippy/extras/tool_probe_endstop.py \
      ~/klipper/klippy/extras/tool_probe.py \
      ~/klipper/klippy/extras/tool.py \
      ~/klipper/klippy/extras/tools_calibrate.py
```

## Printer Config
Remove the following include line from your `printer.cfg`:

``` cfg
[include toolchanger/readonly-configs/toolchanger-include.cfg]
```

## Moonraker Config
If you added the update manager entry during installation, remove the following block from your `moonraker.conf`:

``` cfg
[update_manager klipper-toolchanger-easy]
type: git_repo
path: ~/klipper-toolchanger-easy
origin: https://github.com/jwellman80/klipper-toolchanger-easy.git
managed_services: klipper
primary_branch: main
```

klipper-toolchanger has been removed cleanly from your system.

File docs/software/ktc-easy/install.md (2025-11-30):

## Clone and Install
Connect to the printer via SSH and enter the following commands:

``` bash { .copy }
cd ~/
git clone https://github.com/jwellman80/klipper-toolchanger-easy.git
cd ~/klipper-toolchanger-easy
./install.sh
```

You will be prompted to decide a Z probe solution. A typical StealthChanger uses the built-in tap sensor for probing and option 1 should be chosen.

``` bash
1. I will use the TAP sensor as my Z probe on each tool
2. I will use a shuttle mounted Beacon/Cartographer/Eddy/etc as my Z probe
```

!!! example "Eddy Current"
    Eddy current sensors on StealthChanger have additional requirements and some limitations, they are considered experimental. 

## File Structure
After installation, your configuration will be organized as follows:

```
~/printer_data/config/toolchanger/
├── readonly-configs/           # DO NOT EDIT - Symlinked macros
│   ├── homing.cfg
│   ├── tool_detection.cfg      # TAP install only
│   ├── toolchanger.cfg
│   ├── toolchanger-macros.cfg
│   ├── calibrate-offsets.cfg
│   ├── crash-detection.cfg
│   └── toolchanger-include.cfg
├── tools/                      # Tool-specific configurations
│   ├── example_T0.cfg          # Example configurations
│   └── example_T1.cfg
└── toolchanger-config.cfg      # User-editable overrides
```

## Include Configs
Include the configuration by adding the following to the start of your `printer.cfg`
``` cfg { .copy }
[include toolchanger/readonly-configs/toolchanger-include.cfg]
```

## Moonraker Config
Optional, but recommended, add the following to your `moonraker.conf` to enable automatic updates:

``` cfg { .copy }
[update_manager klipper-toolchanger-easy]
type: git_repo
path: ~/klipper-toolchanger-easy
origin: https://github.com/jwellman80/klipper-toolchanger-easy.git
managed_services: klipper
primary_branch: main
```

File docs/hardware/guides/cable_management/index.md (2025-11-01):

# Cable Management

{% set guides = get_hardware("cable_management") %}
{% include "_templates/guide_cards.md" %}

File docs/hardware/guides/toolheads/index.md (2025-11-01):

# Toolheads

{% set guides = get_hardware("toolheads") %}
{% include "_templates/guide_cards.md" %}

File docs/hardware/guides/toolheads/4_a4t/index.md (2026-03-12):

# A4T

{% set assembly = get_hardware("toolheads")["A4T"] %}

{% include "_templates/overview.md" %}

## Assembly
{% include "_templates/assembly_viewer.md" %}

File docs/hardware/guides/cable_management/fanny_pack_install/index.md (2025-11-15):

# Fanny Pack Install

{% set assembly = get_hardware("cable_management")["Fanny Pack Install"] %}

{% include "_templates/overview.md" %}

## Assembly
{% include "_templates/assembly_viewer.md" %}

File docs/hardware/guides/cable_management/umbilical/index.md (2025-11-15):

# Umbilical

{% set assembly = get_hardware("cable_management")["Umbilical"] %}

{% include "_templates/overview.md" %}

## Assembly
{% include "_templates/assembly_viewer.md" %}

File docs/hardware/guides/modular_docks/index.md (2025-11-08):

# Modular Docks

{% set guides = get_hardware("modular_docks") %}
{% include "_templates/guide_cards.md" %}

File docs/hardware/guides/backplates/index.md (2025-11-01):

# StealthChanger Backplates

{% set guides = get_hardware("backplates") %}
{% include "_templates/guide_cards.md" %}

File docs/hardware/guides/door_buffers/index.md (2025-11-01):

# Door Buffers

{% set guides = get_hardware("door_buffers") %}
{% include "_templates/guide_cards.md" %}

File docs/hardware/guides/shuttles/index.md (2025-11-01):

# Shuttles

{% set guides = get_hardware("shuttles") %}
{% include "_templates/guide_cards.md" %}

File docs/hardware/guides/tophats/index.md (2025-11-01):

# Tophats

{% set guides = get_hardware("tophats") %}
{% include "_templates/guide_cards.md" %}

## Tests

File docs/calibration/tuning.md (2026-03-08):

## Resonance
Typically, each toolhead board will have its own accelerometer for resonance testing. 
Each accelerometer needs to be given a unique name in Klipper so that it can be called directly.

``` cfg title="Example of tool's Nitehawk36 ADXL345 configuration."
[adxl345 T0]
cs_pin: NHK0:gpio27
spi_software_sclk_pin: NHK0:gpio18
spi_software_mosi_pin: NHK0:gpio20
spi_software_miso_pin: NHK0:gpio19
axes_map: x,z,y
```

Klipper's [[resonance_tester]](https://www.klipper3d.org/Config_Reference.html#resonance_tester){target="_blank"} module only supports a single `accel_chip` to be set at a time. This means that any time you want to run input shaper, the accelerometer chip needs to be defined to ensure the correct toolhead board is being used. 

You can swap the accelerometer manually by changing the `accel_chip` in [[resonance_tester]](https://www.klipper3d.org/Config_Reference.html#resonance_tester){target="_blank"}.

``` cfg hl_lines="4" title="Example [input_shaper] & [resonance_tester] sections."
[input_shaper]

[resonance_tester]
accel_chip: adxl345 T0
probe_points: 175,175,20
sweeping_accel: 400
sweeping_period: 0
```

To run input shaper without changing the `accel_chip` in [[resonance_tester]](https://www.klipper3d.org/Config_Reference.html#resonance_tester){target="_blank"}, you can specify the accelerometer in the macro's parameters.

``` lua { .copy title="Shaketune input shaper example." }
AXES_SHAPER_CALIBRATION ACCEL_CHIP="'adxl345 T0'"
```

### Applying the Results
Each tool can have the frequency, shaper type, and damping ratio defined for the X and Y axes in the [[tool Tn]](../software/ktc-easy/configuration/tool.md#tool) section by adding the following parameters:

- `params_input_shaper_freq_x`
- `params_input_shaper_type_x`
- `params_input_shaper_damping_ratio_x`
- `params_input_shaper_freq_y`
- `params_input_shaper_type_y`
- `params_input_shaper_damping_ratio_y`

``` cfg hl_lines="12 13 14 15 16 17" title="Example [tool Tn] section with input shaper"
[tool T0]
tool_number: 0
extruder: extruder
fan: T0_partfan
params_park_x: 5.0   # The absolute X-position of the tool in its dock.
params_park_y: 10.8  # The absolute Y-position of the tool in its dock.
params_park_z: 264.4 # The absolute Z-position where the tool and shuttle mate in the dock,determined when the TAP (or Z-probe) triggers.
gcode_x_offset: 0 # The X-Axis offset of the nozzle's orifice in relation to tool 0
gcode_y_offset: 0 # The Y-Axis offset of the nozzle's orifice in relation to tool 0
gcode_z_offset: 0 # The Z-Axis offset of the nozzle's orifice in relation to tool 0

params_input_shaper_freq_x: 62.2
params_input_shaper_type_x: 'ei'
params_input_shaper_damping_ratio_x: 0.098
params_input_shaper_freq_y: 41.0
params_input_shaper_type_y: 'mzv'
params_input_shaper_damping_ratio_y: 0.088

```

## Tool Change Speed
The speed of a tool change is determined by multiple factors.

1. The size of the printer.
2. The quality of components used.
3. The power given to the motors.
4. `max_velocity` in the `[printer]` section.
5. `max_accel` in the `[printer]` section.
6. `max_z_velocity` in the `[printer]` section.
7. `max_z_accel` in the `[printer]` section.
8. `params_fast_speed` in the `[toolchanger]` section.
9. `params_path_speed` in the `[toolchanger]` section.

The first 2 are choices made while building your printer, make sure to use quality motors and rails from reputable sources. The third depends on which PSU and motor drivers you have, and the rest are all settings that need to be tuned.

### Determining Power
Typically, a good starting point for the `run_current` of your motors is to use 40% of the motor's rated current. For example, if your motor is rated to 2a, `2*0.4=0.8`. Your starting `run_current` would be `0.8`. This can vary depending on the motor or manufacturer, but whether your running 24 or 48 volts, 40% of the motors rated current should yeild good results. 

Increasing the `run_current` could enable faster tool changes, but should be done with caution.

!!! danger "Hot Hot Hot"
    Voron 2.4 motor mounts are made from printed plastic. If they get too hot they will deform, causing catastrophic failure.

    When increasing the `run_current` of your motors, make sure to monitor the temperature of the motors during operation. If the temperature starts to get too hot, reduce the `run_current` and monitor the temperature again.

For more information on tuning your `run_current`, consult [Ellis' Print Tuning guide](https://ellis3dp.com/Print-Tuning-Guide/articles/determining_motor_currents.html){target="_blank"}.

### max_velocity and max_accel
`max_velocity` and `max_accel` are typically tuned as part of standard printer build and determine the maximum limit of how fast your printer can accelerate and move in the the XY axis.

For more information on `max_velocity` and `max_accel`, consult [Ellis' Print Tuning guide](https://ellis3dp.com/Print-Tuning-Guide/articles/determining_max_speeds_accels.html){target="_blank"}.

### max_z_velocity and max_z_accel
`max_z_velocity` and `max_z_accel` are typically overlooked on a standard printer build, but are rather important for StealthChanger. They determine the maximum limit of how fast your printer can accelerate and move in the the Z axis.

The standard Voron 2.4 example configurations are intentionally conservative regarding gantry Z movement speeds—and for good reason. If any one of the four Z-axis motors were to skip steps while the others continue to move, the gantry would become racked.

With StealthChanger, the gantry operates at significantly higher speeds than most stock configurations. If a Z-axis motor were to skip at these elevated speeds, the resulting misalignment of the gantry corners could be severe enough to cause significant damage to the gantry.

!!! warning "Flying too close to the sun"
    This is an example of what could happen if you tune your configuration too fast for the hardware you are using. Thanks to fireishott on Discord for the image.

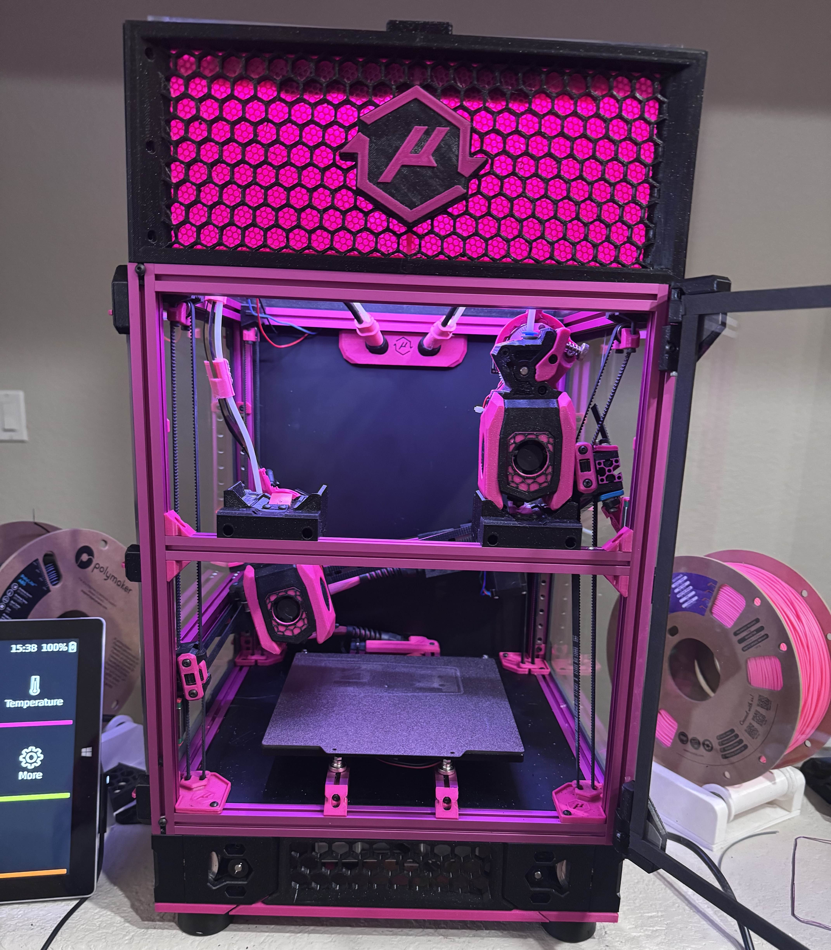
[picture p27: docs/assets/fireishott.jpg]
fireishot
    

#### Increasing Z speeds
Increasing the `max_z_velocity` and `max_z_accel` values should only be done once you are able to do tool changes and should be done in small increments.

``` cfg title="[printer] section example."
[printer]
kinematics: corexy
max_velocity: 300
max_accel: 3000
max_z_velocity: 100
max_z_accel: 1000 # Start with 500 for G2Z.
square_corner_velocity: 5.0
```

- Increase your `max_z_accel` in increments of 100-200 at a time. Test with multiple tool changes between increments.
- Increase your `max_z_velocity` in increments of 25-50 at a time. Test with multiple tool changes between increments.

#### Z-Axis Speed Calculator

{% include "_templates/z_speed_calc.md" %}

### params_fast_speed and params_path_speed
`params_fast_speed` and `params_path_speed` are klipper-toolchanger's way of limiting the speeds used for tool changes and are located in the [`[toolchanger]`](../software/ktc-easy/configuration/toolchanger.md#toolchanger) section of the [toolchanger-config](../software/ktc-easy/configuration/toolchanger.md). 

- `params_fast_speed` clamps the all movements to the dock at it's set value.
- `params_path_speed` clamps the all of the pickup or dropoff movements within the dock at it's set value.

``` cfg hl_lines="8 9" title="[printer] section example."
[toolchanger]
# These paths have been verified to work with StealthChanger with ModularDock, it should not be changed unless you understand what you are doing.
params_dropoff_path: [{'y':9.5 ,'z':4}, {'y':9.5, 'z':2}, {'y':5.5, 'z':0}, {'z':0, 'y':0, 'f':0.5}, {'z':-10, 'y':0}, {'z':-10, 'y':16}]
params_pickup_path: [{'z':-10, 'y':16}, {'z':-10, 'y':0}, {'z':0, 'y':0, 'f':0.5, 'verify':1}, {'y':5.5, 'z':0}, {'y':9.5, 'z':2}, {'y':9.5 ,'z':4}]

params_safe_y: 120 # The distance from absolute zero to the back of the tools in the dock. Allow some extra clearance.
params_close_y: 30 # The relative distance from safe_y the gantry moves to while changing tools.
params_fast_speed: 10000 # Movement speed while outside of the dock during tool changes.
params_path_speed: 900 # Movement speed used for pickup and dropoff during tool changes.
```

Increasing these values will result in faster tool change movement up to the point of reaching your `max_velocity`, `max_accel`, `max_z_velocity` and `max_z_accel` values. The `max_velocity`, `max_accel`, `max_z_velocity` and `max_z_accel` values will be used if `params_fast_speed` or `params_path_speed` exceeds them.

### Deminishing Returns
After tuning all of your currents and speeds, a typical Voron 2.4 should be capable of tool changes that are less than 10 seconds from the bed and back. 

With specialized hardware, faster speeds can be achieved, but you get to the point where there is little to no benifit. As per [Prusa's Max Speed Calculator](https://blog.prusa3d.com/calculator_3416/#speed), you can only accelerate so fast until reaching the maximum velocity. With the size of the standard Voron 2.4 being 350mm or less, you start to be limited by the time it takes to actually pickup the tool. 

You need to allow enough time for the StealthChanger Shuttle and Backplate to engage cleanly and the OptoTap sensor to detect the presence of the Backplate. Klipper-toolchanger has hardcoded pauses to allow for these things to happen reliably and can not be adjusted by the end user.

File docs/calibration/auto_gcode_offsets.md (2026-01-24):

Automated calibration uses specialized tools to measure X/Y/Z offsets more precisely and efficiently. Refer to each tool's documentation for specific calibration procedures.

## Available Methods

{% for method, data in cal_methods.items() %}
{% if method != "Manual" %}
- **[{{ method }}]({{ data.url|relative_url }}){% if data.url.startswith("http") %}{:target="_blank"}{% endif %}** – {{ data.description }}
{% endif %}
{% endfor %}

## Calibration With SexBall Probe

### Define Switch Location
With the SexBall Probe mounted to the printer's bed extrusion, the absolute position of the ball needs to be added to the [[gcode_macro _CALIBRATION_SWITCH]](../software/ktc-easy/configuration/toolchanger.md#gcode_macro-_calibration_switch) variables.

``` cfg title="Calibration switch variables example." hl_lines="2 3 4"
  [gcode_macro _CALIBRATION_SWITCH]
  variable_x: 227.471875
  variable_y: 353.703125
  variable_z: 5.00
  gcode:
```

1. Home the printer with `G28`.
2. Run `QUAD_GANTRY_LEVEL` to level the gantry.
3. Home z again with `G28 Z`.
4. Manually move the gantry so that the tool is ~1mm over the ball.
5. Run `M114` to output the current position to console.
6. Enter the positions in to the [[gcode_macro _CALIBRATION_SWITCH]](../software/ktc-easy/configuration/toolchanger.md#gcode_macro-_calibration_switch) variables.

### Enable Multi Axis Probing
- Enable the multi-axis probe by defining the [[tools_calibrate]](../software/ktc-easy/configuration/toolchanger.md#tools_calibrate) section in [toolchanger-config.cfg](../software/ktc-easy/configuration/toolchanger.md).
- Set the `pin` variable to the pin that your calibration probe is connected to.
- Calibrate `trigger_to_bottom_z`

``` cfg title="[tools_calibrate] example."
  [tools_calibrate]
  pin:   #pin that your calibration probe is connected to.
  travel_speed: 20  # mms to travel sideways for XY probing
  spread: 7  # mms to travel down from top for XY probing
  lower_z: 1.0  # The speed (in mm/sec) to move tools down onto the probe
  speed: 2  # The speed (in mm/sec) to retract between probes
  lift_speed: 4  # Z Lift after probing done, should be greater than any Z variance between tools
  final_lift_z: 6 
  sample_retract_dist:2
  samples_tolerance:0.05
  samples:5
  samples_result: median # median, average
  probe: probe # name of the nozzle probe to use
  trigger_to_bottom_z: 0.25 # Offset from probe trigger to vertical motion bottoms out. 
```

!!! tip "trigger_to_bottom_z"
    `trigger_to_bottom_z` is the travel distance from the point where the nozzle touches the top of the ball to the point where the switch not only triggers, but bottoms out.

    1. Move the gantry so that the nozzle touches the top of the ball.
    2. Using small increments, lower the gantry until you hear the switch trigger.
    3. Run `M114` to log the gantry's current position to the console.
    4. Watching the tool on the shuttle, continue to lower the gantry. The point where the tool starts to lift, is the point where the switch has bottomed out.
    5. Run `M114` again and the difference between the 2 logged values is your `trigger_to_bottom_z` value.

### SexBall Nozzle Calibration

1. Any debris on the tool will effect the accuracy of the results. Clean all of the tool's nozzles thoroughly. 
2. With tool 0 on the shuttle, home the printer with `G28`.
3. Run `QUAD_GANTRY_LEVEL` to level the gantry.
4. Home Z again with `G28 Z`.
5. With your hand over the emergency stop, run `CALIBRATE_ALL_OFFSETS`.

!!! info "CALIBRATE_ALL_OFFSETS"
    `CALIBRATE_ALL_OFFSETS` will move the tool over the probe and heat it to 150c before locating the probe. For the first run keep an eye on the printer and make sure the values entered in the config are correct and there isn't a crash.

    After tool 0 has located the probe, it will turn off tool 0's heater and repeat the process for each subsequent tool. Tool 0 will be picked up again once the process has completed.

    The values logged to the console are the offsets for `T1+` to be used in the `[tool Tn]`'s `gcode_x_offset`, `gcode_y_offset` and `gcode_z_offset` variables.
    All of the `gcode_offsets` for `T0` should remain `0`.

### SexBall Probe Z Offset Calibration

1. Any debris on the tool will effect the accuracy of the results. Clean all of the tool's nozzles thoroughly. 
2. With tool 0 on the shuttle, home the printer with `G28`.
3. Run `QUAD_GANTRY_LEVEL` to level the gantry.
4. Home z again with `G28 Z`.
5. Run `CALIBRATE_NOZZLE_PROBE_OFFSET`.

!!! info "CALIBRATE_NOZZLE_PROBE_OFFSET"
    `CALIBRATE_NOZZLE_PROBE_OFFSET` will move the tool over the probe and heat it to 150c before locating the probe. It will then bottom out the probe and use the tool's OptoTap sensor to determine the `[tool_probe Tn]`'s `z_offset`.

    The value logged to the console is the value to be used for the `[tool_probe Tn]`'s `z_offset`.

!!! warning "Don't Trust the Robots"
    The `[tool_probe Tn]` `z_offset` should be verified using a small test print. Because this procedure depends on the accuracy of the `trigger_to_bottom_z` value, it is advisable to confirm the offset by performing a short test print and noting any adjustments required to achieve proper first-layer adhesion.

    - If you need to raise the nozzle during the test print, the `z_offset` must be adjusted closer to zero by the same amount.
    - If you need to lower the nozzle during the test print, the `z_offset` must be adjusted farther from zero by the same amount.

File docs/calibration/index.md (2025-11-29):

# Calibration Overview
StealthChanger calibration consists of three primary stages: [Probe Offset](#probe-offset), [Dock Positions](#dock-positions), and [G-code Offsets](#g-code-offsets).

## Important Notes 
=== "TAP"
    - **Only home/QGL/bedmesh with tool 0.** — Homing with other tools should only be done in order to switch to tool 0 which then can be used to home (again)/QGL/bedmesh.
    - **The `gcode_z_offset`, `gcode_x_offset` and `gcode_y_offset` variables for tool 0 must always be zero.** — The offset values are relative to tool 0.

    !!! warning "Before You Start"
        - Because all G-code calibrations are relative to tool 0, it is essential that the printer has perfect first layer bed adhesion with tool 0 first.
        - It is recommended that you run a test print with tool 0 before calibrating any G-code offsets.

=== "Eddy Current"
    - **Home/QGL/bedmesh is possible with any tool** — Requires the scanner to be mounted on the shuttle.
    - **`gcode_z_offset` variable must be set for every tool** — Homing with the scanner on the shuttle requires each nozzle to have a z offset relative to the scanner.
    - **`gcode_x_offset` and `gcode_y_offset` variables for tool 0 must always be zero.** — The offset values are relative to tool 0.

    !!! warning "Before You Start"
        - It is essential that the printer has perfect first layer bed adhesion with tool 0 first.
        - It is recommended that you run a test print with tool 0 before calibrating any G-code offsets.

## Probe Offset
Probe offset refers to the `[tool_probe]` parameter `z_offset` which is applied whenever the printer homes or performs bed leveling. This value represents the vertical distance between the probe’s trigger point and the nozzle tip, allowing Klipper to accurately determine the true Z=0 position for a given tool. A `z_offset` must be calibrated for T0, and for any additional tool that will be used for homing.

!!! info "I'm building all my tools from the same hardware"
    Even when using identical hardware, each tool may require a unique `z_offset` due to:

    - Variations in hardware components.
    - Differences resulting from printing or assembly tolerances.
    - Slight deviations between the nozzle’s physical zero point and the probe’s trigger point.

Accurate `z_offset` values ensure consistent and reliable first-layer performance across all tools.

## Dock Positions
Dock Positions refers to the `[tool Tn]` parameters `params_park_x`, `params_park_y`, and `params_park_z`. These values tell the printer the precise coordinates required to pick up or return a tool to its designated dock. In essence, a dock position defines the exact X/Y/Z point where the shuttle aligns with a tool so that the mechanical coupling can occur reliably. You can think of it as the tool’s pickup location for its specific dock.

Each tool requires its own dock position because the docks are mounted at different locations along the front of the printer. Even small variations in mounting or alignment can cause the shuttle to miss the tool or collide with the dock.

When dock positions are accurately calibrated, tool changes are consistent, repeatable, and free from collisions.

!!! tip "Calibrate you printer first"
    Before setting dock positions, it is strongly recommended to calibrate your printer’s zero point.

    Dock positions are defined relative to absolute zero—if the printer’s zero point changes, the dock positions will shift accordingly.

## G-code Offsets

G-code offsets refers to the `[tool Tn]` parameters `gcode_z_offset`, `gcode_x_offset` and `gcode_y_offset`. These values determine the difference in the nozzle's position for each tool when it is on the shuttle, relative to T0. 

!!! info "Why G-code offsets matter"
    When the slicer generates `G1 X100 Y100`, every tool should deposit filament at exactly the same physical location on the bed. G-code offsets make this possible by telling Klipper "this tool is 0.2mm left and 0.1mm forward off the reference tool, so adjust accordingly."

### G-code Offset Calibration Methods
There are multiple methods of calibrating the G-code offsets, 

{% for method, data in cal_methods.items() %}
- **[{{ method }}]({{ data.url|relative_url }}){% if data.url.startswith("http") %}{:target="_blank"}{% endif %}** – {{ data.description }}
{% endfor %}

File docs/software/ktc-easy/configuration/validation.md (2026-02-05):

!!! failure "Klipper Error"
    If you are experiencing Klipper errors after setting up your toolchanger-config and T0 config, please consult [Software Troubleshooting](../../troubleshooting.md).

## Pre Launch
Before configuring and calibrating the other tools, it is advised to get the printer printing with tool 0 before continuing configuration of everything else. Before homing and starting a print, there are some checks we should do to make sure everything behaves as intended.

### Hardware Checks
Make sure your toolhead passes all of the following checks before continuing.

1. When you place the tool on the shuttle the OptoTap sensor triggers its LED.
2. Validate that the tool is being detected by running `INITIALIZE_TOOLCHANGER` with, and without the tool on the shuttle. You should get confirmation that the tool has been detected when the tool is on the shuttle. It should also report `active tool: none` if no tools was detected.
3. Once the tool detected test the part cooling fans turn on with `M106 S127` and off with `M107`.
4. The hotend heats up and the hotend fan turn on with `M104 S200` and off with `M104 S0`.
5. Once at temperature, the extruder motor moves with `G1 E100 F100`.
6. Finally, turn the hotend off with `M104 S0`

If any of these steps fails, the issue could be either hardware or software related. Consult the [Hardware Troubleshooting](../../../hardware/troubleshooting.md) and [Software Troubleshooting](../../troubleshooting.md).

### Tool detection and homing
1. Check that the tool detection is working by running `INITIALIZE_TOOLCHANGER` with, and without the tool on the shuttle. You should get confirmation that the tool either was or wasn't detected.
2. With the tool on the shuttle, home the Y axis by running `G28 Y`.
3. Run `G28 X`.
4. Run `G28 Z`.

!!! success
    At this point the printer should be homed and everything is running as intended. 
    
    If you have any issues initializing or homing, please consult [Software Troubleshooting](../../troubleshooting.md).

### Backplate Break In
Because the StealthChanger’s action relies on precisely fitted pins and bushings, it’s a good idea to operate the mechanism repeatedly to allow the components to seat properly. This break-in process should be performed for every tool.

!!! note "TAP Only"
    This method only works for TAP probing.

1. Heatsoak your printer.
2. Run `G28`
3. Run `QUAD_GANTRY_LEVEL`
3. Run `G28 Z`
2. Run `PROBE_ACCURACY SAMPLES=100`

!!! failure "Failure"
    If you experience failure during this step or you feel the accuracy is not as good as it should be, consult the [Hardware Troubleshooting](../../../hardware/troubleshooting.md) section.

{% include "_templates/probe_offset.md" %}

## First Print
If you copied your [extruder] values from a previous config, you are ready for your first print. If your setting up the printer for the first time, you may need to PID tune your hotend and tune your extruder first.

!!! tip "Extruder Tuning"
    For PID tuning we recommend [Voron's PID Tuning Guide](https://docs.vorondesign.com/build/startup/startup.html?model=v2&step=11&interface=mainsail&probe=tap){:target="_blank"}.

    For extruder calibration we recommend [Ellis' Extruder Calibration Guide](https://ellis3dp.com/Print-Tuning-Guide/articles/extruder_calibration.html){:target="_blank"}.

Run a print as you would for any standard printer first print. As long as the tool is on the shuttle, the printer will behave as any other TAP based printer.

!!! question "Is that it?"
    Getting a single tool printing is much the same as any other printer. We shouldnt bother ourselves with any tool offsets or park positions just yet.

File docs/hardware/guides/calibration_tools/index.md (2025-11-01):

# Calibration Tools

{% set guides = get_hardware("calibration_tools") %}
{% include "_templates/guide_cards.md" %}

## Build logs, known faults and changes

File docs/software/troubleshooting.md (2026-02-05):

## Common Issues

### HomingViaProbeHelper.__init__() takes 4 positional arguments but 5 were given
Update Klipper to the latest version. Klipper-toolchanger-easy requires Klipper 0.13.0-457 or greater.

### HomingViaProbeHelper.__init__() missing 1 required positional argument: 'param_helper'

!!! info "UPDATE"
    As of 4 Feb 2026 klipper-toolchanger-easy has been updated to support the changes made to probe in Klipper. Update klipper-toolchanger-easy to the latest version to resolve this issue. 

Klipper made changes 25 Jan 2026 to probe that require klipper-toolchanger to be updated. You can revert Klipper to before the breaking changes by running the following commands in terminal.

``` bash {.copy}
    sudo service klipper stop
    cd ~/klipper
    git checkout e605fd18560fbb5a7413ca12b72325ad4e18de16
    sudo service klipper start
```

### INITIALIZE_TOOLCHANGER - Tool Not Recognized
- Check that you have the correct pin assigned to the OptoTap sensor.
- If the tool initializes while off the shuttle, the logic is flipped. Either add or remove `!` to the pin definition.
- Some OptoTap sensors require a pullup to operate. Try adding a `^` to the pin definition.
- Check wring/crimps.

---

### INITIALIZE_TOOLCHANGER - Wrong Tool Recognized
- Check the `tool_number` assignment in the [[tool]](ktc-easy/configuration/tool.md#tool) section.

---

### Wrong hotend fan turns on
- Check the `extruder` assignment in the [[heater_fan]](ktc-easy/configuration/tool.md#heater_fan) section.

---

### Wrong part fans turn on
- Check the `fan` assignment in the [[tool]](ktc-easy/configuration/tool.md#tool) section.

---

### Wrong hotend heats up
- Check the `extruder` assignment in the [[tool]](ktc-easy/configuration/tool.md#tool) section.
- Check the `activate_gcode` extruder in the [[tool_probe]](ktc-easy/configuration/tool.md#tool_probe) section.

---

### Wrong extruder moves
- Check the `extruder` assignment in the [[tool]](ktc-easy/configuration/tool.md#tool) section.
- Check the `extruder` name of the [[tmc2209]](ktc-easy/configuration/tool.md#tmc2209) section.

---

### Heater extruder1 not supported
- are you using elis bed fan macro's?
- at line 53 of [bedfans.cfg](https://github.com/VoronDesign/VoronUsers/blob/8e5067f4f6457da8a552983dd210ec48c40be2ca/printer_mods/Ellis/Bed_Fans/Klipper_Macros/bedfans.cfg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){:target="_blank"}
- change it from `{action_respond_info("Heater %s not supported" % HEATER)}` to `_SET_HEATER_TEMPERATURE {rawparams}`
 
 Big thank you to BrewNinja on Discord for sharing this fix.

---

{% include "_templates/community_help.md" %}

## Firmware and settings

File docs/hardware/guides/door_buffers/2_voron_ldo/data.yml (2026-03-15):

title: Door Buffer (LDO Version)
author: "DraftShift Design"
summary: >
    The LDO version of Door Buffer for Voron 2.4.
  
    !!! tip "Where can I get one?"
        The hardware components for this guide are all included as a part of LDO's [StealthChanger Tophat and Door Buffer Kit](../../../../resellers.md).

    !!! info "Short/Standard?"
        There are different printed files depending on whether you are using short Modular Docks or Standard. If you are unsure, consult the [Tools Section](../../../toolheads.md) for compatibility.

    !!! info "LDO Door"
        The LDO Door Buffer expects that you will be using the LDO door as indicated in their Voron V2.4 Guide. You can find it [here](https://github.com/MotorDynamicsLab/LDOVoron2/tree/main/STLs/LDO%20Door){target="_blank"}.

printed_bom:
  LDO 300 Short:
    qty: 1 of each
    urls: 
      Bottom Left: "https://github.com/MotorDynamicsLab/LDOStealthChanger/blob/master/STLs/Door%20Buffer/300-short/bottom_left_300s.stl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"
      Bottom Right: "https://github.com/MotorDynamicsLab/LDOStealthChanger/blob/master/STLs/Door%20Buffer/300-short/bottom_right_300s.stl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"
      Top Left: "https://github.com/MotorDynamicsLab/LDOStealthChanger/blob/master/STLs/Door%20Buffer/300-short/top_left_300s.stl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"
      Top Right: "https://github.com/MotorDynamicsLab/LDOStealthChanger/blob/master/STLs/Door%20Buffer/300-short/top_right_300s.stl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"
      Top Mid: "https://github.com/MotorDynamicsLab/LDOStealthChanger/blob/master/STLs/Door%20Buffer/300-short/top_mid_300s.stl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"
      Bottom Mid: "https://github.com/MotorDynamicsLab/LDOStealthChanger/blob/master/STLs/Door%20Buffer/300-short/bottom_mid_300s.stl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"
      Left Mid: "https://github.com/MotorDynamicsLab/LDOStealthChanger/blob/master/STLs/Door%20Buffer/300-short/left_mid_300s.stl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"
      Right Mid: "https://github.com/MotorDynamicsLab/LDOStealthChanger/blob/master/STLs/Door%20Buffer/300-short/right_mid_300s.stl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"
  LDO 300 Standard:
    qty: 1 of each
    urls: 
      Bottom Left: "https://github.com/MotorDynamicsLab/LDOStealthChanger/blob/master/STLs/Door%20Buffer/300/bottom_left_300.stl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"
      Bottom Right: "https://github.com/MotorDynamicsLab/LDOStealthChanger/blob/master/STLs/Door%20Buffer/300/bottom_right_300.stl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"
      Top Left: "https://github.com/MotorDynamicsLab/LDOStealthChanger/blob/master/STLs/Door%20Buffer/300/top_left_300.stl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"
      Top Right: "https://github.com/MotorDynamicsLab/LDOStealthChanger/blob/master/STLs/Door%20Buffer/300/top_right_300.stl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"
      Top Mid: "https://github.com/MotorDynamicsLab/LDOStealthChanger/blob/master/STLs/Door%20Buffer/300/top_mid_300.stl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"
      Bottom Mid: "https://github.com/MotorDynamicsLab/LDOStealthChanger/blob/master/STLs/Door%20Buffer/300/bottom_mid_300.stl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"
      Left Mid: "https://github.com/MotorDynamicsLab/LDOStealthChanger/blob/master/STLs/Door%20Buffer/300/left_mid_300.stl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"
      Right Mid: "https://github.com/MotorDynamicsLab/LDOStealthChanger/blob/master/STLs/Door%20Buffer/300/right_mid_300.stl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"
  LDO 350 Short:
    qty: 1 of each
    urls: 
      Bottom Left: "https://github.com/MotorDynamicsLab/LDOStealthChanger/blob/master/STLs/Door%20Buffer/350-short/bottom_left_350s.stl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"
      Bottom Right: "https://github.com/MotorDynamicsLab/LDOStealthChanger/blob/master/STLs/Door%20Buffer/350-short/bottom_right_350s.stl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"
      Top Left: "https://github.com/MotorDynamicsLab/LDOStealthChanger/blob/master/STLs/Door%20Buffer/350-short/top_left_350s.stl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"
      Top Right: "https://github.com/MotorDynamicsLab/LDOStealthChanger/blob/master/STLs/Door%20Buffer/350-short/top_right_350s.stl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"
      Top Mid: "https://github.com/MotorDynamicsLab/LDOStealthChanger/blob/master/STLs/Door%20Buffer/350-short/top_mid_350s.stl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"
      Bottom Mid: "https://github.com/MotorDynamicsLab/LDOStealthChanger/blob/master/STLs/Door%20Buffer/350-short/bottom_mid_350s.stl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"
      Left Mid: "https://github.com/MotorDynamicsLab/LDOStealthChanger/blob/master/STLs/Door%20Buffer/350-short/left_mid_350s.stl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"
      Right Mid: "https://github.com/MotorDynamicsLab/LDOStealthChanger/blob/master/STLs/Door%20Buffer/350-short/right_mid_350s.stl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"
  LDO 350 Standard:
    qty: 1 of each
    urls: 
      Bottom Left: "https://github.com/MotorDynamicsLab/LDOStealthChanger/blob/master/STLs/Door%20Buffer/350/bottom_left_350.stl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"
      Bottom Right: "https://github.com/MotorDynamicsLab/LDOStealthChanger/blob/master/STLs/Door%20Buffer/350/bottom_right_350.stl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"
      Top Left: "https://github.com/MotorDynamicsLab/LDOStealthChanger/blob/master/STLs/Door%20Buffer/350/top_left_350.stl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"
      Top Right: "https://github.com/MotorDynamicsLab/LDOStealthChanger/blob/master/STLs/Door%20Buffer/350/top_right_350.stl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"
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

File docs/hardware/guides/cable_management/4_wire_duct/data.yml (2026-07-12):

title: Wire Duct
author: "DraftShift Design"
summary: >
    This guide will walk you through the assembly of the Wire Duct. 

    !!! tip "Scaled to fit"
        The Wire Duct Connector needs to be scaled to suit your build. It can be scaled in the slicer.

printed_bom:
  Wire Duct Base:
    qty: 1
    urls:
      Link: https://github.com/DraftShift/CableManagement/blob/main/STLs/WireDuct/wire_duct_base.stl?raw=true
  Wire Duct Cover:
    qty: 1
    urls:
      Link: https://github.com/DraftShift/CableManagement/blob/main/STLs/WireDuct/%5Ba%5D_wire_duct_cover.stl?raw=true
  Wire Duct EMS:
    qty: 1
    urls:
      Link: https://github.com/DraftShift/CableManagement/blob/main/STLs/WireDuct/wire_duct_ft-ems.stl?raw=true
  Wire Duct Connector:
    qty: 1 (Scale to fit)
    urls:
      Link: https://github.com/DraftShift/CableManagement/blob/main/STLs/WireDuct/%5Ba%5D_wire_duct_connector_scale_to_fit.stl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
  Center Rear Skirt:
    qty: 1
    urls:
      Voron 250: https://github.com/DraftShift/CableManagement/blob/main/STLs/WireDuct/v2_skirt/center_rear_skirt_250.stl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
      Voron 300: https://github.com/DraftShift/CableManagement/blob/main/STLs/WireDuct/v2_skirt/center_rear_skirt_300.stl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
      Voron 350: https://github.com/DraftShift/CableManagement/blob/main/STLs/WireDuct/v2_skirt/center_rear_skirt_350.stl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
  90 Degree Adaptor:
    qty: 1
    urls:
      Link: https://github.com/DraftShift/CableManagement/blob/main/STLs/WireDuct/center_rear_skirt_90.stl?raw=true
  EMS Brackets:
    qty: Optional
    urls:
      Arduino Uno: https://github.com/DraftShift/CableManagement/blob/main/STLs/WireDuct/EMS_Brackets/%5Ba%5D_ft-ems_uno_r3.stl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
      WLED Board: https://github.com/DraftShift/CableManagement/blob/main/STLs/WireDuct/EMS_Brackets/WLED.stl?raw=true

hardware_bom:
  M3x6 BHCS Screws:
    qty: 4
  M3x10 BHCS Screws:
    qty: 2
  M3x8 SHCS Screws:
    qty: 4
  M3 Hex Nuts:
    qty: 6
  M3 T-Nuts:
    qty: 2
  M3 Hammerhead Nuts:
    qty: 2

resources:
  DraftShift Cable Management Github: https://github.com/DraftShift/CableManagement

primary_parts:
  - "Center Skirt"
  - "90 Center Rear Skirt"
  - "Fanny Pack Base"
  - "Wire Duct Base"
  - "Wire Duct EMS"

accent_parts:
  - "Hexa Bracket"
  - "WLED EMS"
  - "Wire Duct Connector"
  - "Wire Duct Connector Scaled"
  - "Wire Duct Cover"

frame_parts:
  - "Frame"

steps:
  - description: "Attach the EMS grill to the Wire Duct Base using 4 M3x6 BHCS screws and M3 nuts."
    camera:
      azimuth: 276
      polar: 110
      distance: 27
      pan_x: -0.52
      pan_y: -0.50
    visible: 
      - "Duct Base M3 Nuts"
      - "EMS Grill M3x6 BHCS"
      - "Wire Duct Base"
      - "Wire Duct EMS"
    focus: 
      - "Duct Base M3 Nuts"
      - "EMS Grill M3x6 BHCS"

  - description: "If you have an EMS mount to attach to the EMS grill, do so now."
    camera:
      azimuth: 272
      polar: 94
      distance: 18
      pan_x: 0.15
      pan_y: 0.34
    visible: 
      - "Duct Base M3 Nuts"
      - "EMS Grill M3x6 BHCS"
      - "Wire Duct Base"
      - "Wire Duct EMS"
      - "WLED EMS"
      - "WLED Hardware"
    focus: 
      - "WLED EMS"
      - "WLED Hardware"

  - description: "Attach the Wire Duct Base to the underside of the Fanny Pack using 2 M3x10 BHCS screws."
    camera:
      azimuth: 283
      polar: 115
      distance: 35
      pan_x: 0.99
      pan_y: -1.63
    visible: 
      - "Duct Base M3 Nuts"
      - "EMS Grill M3x6 BHCS"
      - "Wire Duct Base"
      - "Wire Duct EMS"
      - "WLED EMS"
      - "WLED Hardware"
      - "Fanny Pack Base"
      - "FannyPack Hardware"
      - "Hexa Bracket"

      - "Duct Base M3x10 BHCS"
      - "Panel"
      - "Frame"
    focus: 
      - "Duct Base M3x10 BHCS"

  - description: "Attach the Rear Center Skirt using 2 M3x8 SHCS screws and T-Nuts."
    camera:
      azimuth: 277
      polar: 153
      distance: 35
      pan_x: 0.51
      pan_y: -10.25
    visible: 
      - "Duct Base M3 Nuts"
      - "EMS Grill M3x6 BHCS"
      - "Wire Duct Base"
      - "Wire Duct EMS"
      - "WLED EMS"
      - "WLED Hardware"
      - "Fanny Pack Base"
      - "FannyPack Hardware"
      - "Hexa Bracket"
      - "Duct Base M3x10 BHCS"
      - "Panel"
      - "Frame"
      - "Center Skirt"
      - "Skirt M3x8 SHCS Vertical"
      - "Skirt T-Nuts"
    focus: 
      - "Skirt M3x8 SHCS Vertical"
      - "Skirt T-Nuts"

  - description: "Install 2 M3x8 SHCS screws with hammerhead nuts into the 90 Degree Adapter."
    camera:
      azimuth: 61
      polar: 67
      distance: 19
      pan_x: -0.63
      pan_y: -1.47
    visible: 
      - "90 Center Rear Skirt"
      - "Skirt M3x8 SHCS Horizontal"
      - "M3 Hammerhead Nuts"
    focus: 
      - "Skirt M3x8 SHCS Horizontal"
      - "M3 Hammerhead Nuts"
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

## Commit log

2025-11-06 Prelim cable management
2025-11-08 Added frames and blockers to dock build guides
2025-11-14 reseller added sponsor, and configurator buttons
2025-11-15 Cable Management Models
2025-11-15 Update Umbilical Plate Guide
2025-11-18 Mellow canbus expand board
2025-11-20 Added steps to wire duct and updated viewer.
2025-11-20 Assembly overview icons.
2025-11-21 Add FAQ to stealthchanger.md. Add 2nd backplate heat treatment option to troubleshooting guide as collapsible entry.
2025-11-22 Add FAQ page and a note to loosen screw before trying the soldering iron heat treatment option.
2025-11-23 Complete Wire Duct Assembly
2025-11-28 Calibration Refresh
2025-11-28 Split G-code offsets calibration in to two sections.
2025-11-29 Calibration Corrections
2025-11-30 tweak sc assembly guide and add less compressed model to ease off clientside decompress, move it in nav, rename overviews in nav
2025-12-30 probe_offset.md: fix spelling
2026-01-05 switch tap PCB mounting to M3x6mm screws rather than 8mm.
2026-01-05 Mention spacing the belts evenly.
2026-01-05 Change wording for wire duct cover.
2026-01-05 Revert "tool_boards.yml - clarify EBB36 and EBB42 nomenclature"
    This reverts commit 16975ab3478b5513acd192130a048bf04a4e6929.
    [tool_boards.yml]
2026-01-17 Fix assembly viewer conflict with usermods
2026-01-25 Add latest probe breakage instructions
2026-01-30 Add tool detection validation step to toolhead checks
    Add step to validate tool detection by running INITIALIZE_TOOLCHANGER with and without the tool on the shuttle. Renumber subsequent validation steps accordingly.
2026-02-05 klipper-toolchanger-easy update notice
2026-02-05 Add update recommendation for older klipper install
2026-02-05 Revert "Add update recommendation for older klipper install"
    This reverts commit 5cf913399d2c825fe66c17b7870d7a56f87a56f6.
2026-02-05 Revert "klipper-toolchanger-easy update notice"
    This reverts commit c9bc9e9b023304b461ba9abdbe8e10bd823ab8b1.
2026-02-05 Reapply "klipper-toolchanger-easy update notice"
    This reverts commit 462bce8b50bedff87a271a7db7948dcbcd22c892.
2026-02-05 Reapply "Add update recommendation for older klipper install"
    This reverts commit 254ae3c324b31f066cb19213f2f3df0cc0bb6b92.
2026-02-08 Switch to weekly usermod updates
2026-02-16 EBB36 V2 config fixes
    [example_boards.yml]
2026-04-03 InputShaper comment out values, and set them at 50Hz
2026-04-04 Change detection pin for EBB36 V1.2
